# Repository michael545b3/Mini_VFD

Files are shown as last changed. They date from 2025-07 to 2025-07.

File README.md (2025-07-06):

# Mini VFD based on STM32

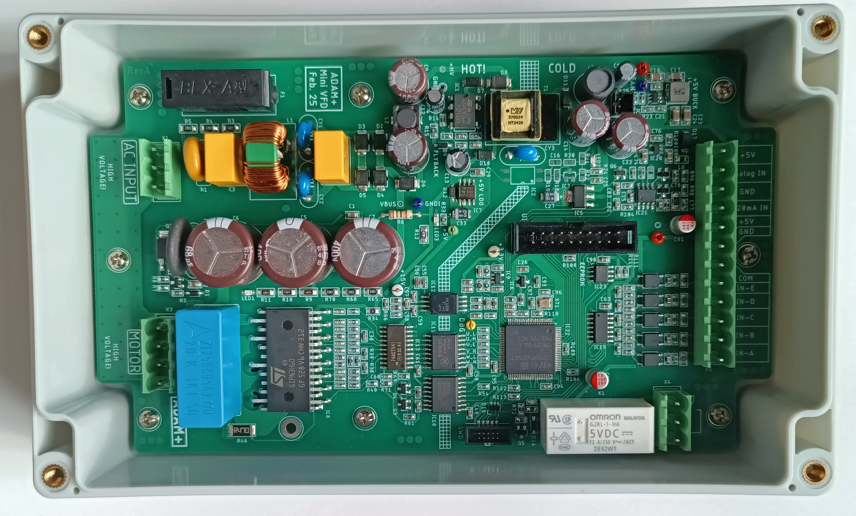
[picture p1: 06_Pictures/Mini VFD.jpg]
Mini VFD


This project is a compact Variable Frequency Drive (VFD) built around an  
STM32 microcontroller and an ST IPM (Intelligent Power Module).  
It is designed to control small AC motors efficiently and safely in a compact form factor.

---

## Hardware Overview

### Core Components
- **STM32F407** microcontroller
- **STGIPN3H60** IPM (Intelligent Power Module)
- **High-voltage measurement**
- **Analog inputs** for control signals
- **Opto-isolated digital inputs**
- **Relay output**
- **EEPROM** for parameter storage

### Power Supply
- **Flyback converter** for isolated supply
- **E-Fuse** for protection
- **Buck converter** with **LDOs** for logic power

### User Interface
- **LCD display**
- **Push buttons** and **rotary encoder** for input

---

## Software Status

The firmware is currently under development. As a hardware-focused developer,  
progress is steady but slow — writing robust embedded software takes time.

So far, the implemented functions run reliably, and more features are being added continuously.  
A demonstration video will be available soon.

---

## Roadmap / To-Do

- [ ] Motor control tuning
- [ ] UI menu system improvements
- [ ] Fault monitoring and protection
- [ ] IO implementation

---

## Contributions

Contributions, feedback, or suggestions are very welcome!

---

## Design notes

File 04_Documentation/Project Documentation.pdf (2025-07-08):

# Mini VFD

Michael Adam
michael.adam4@proton.me

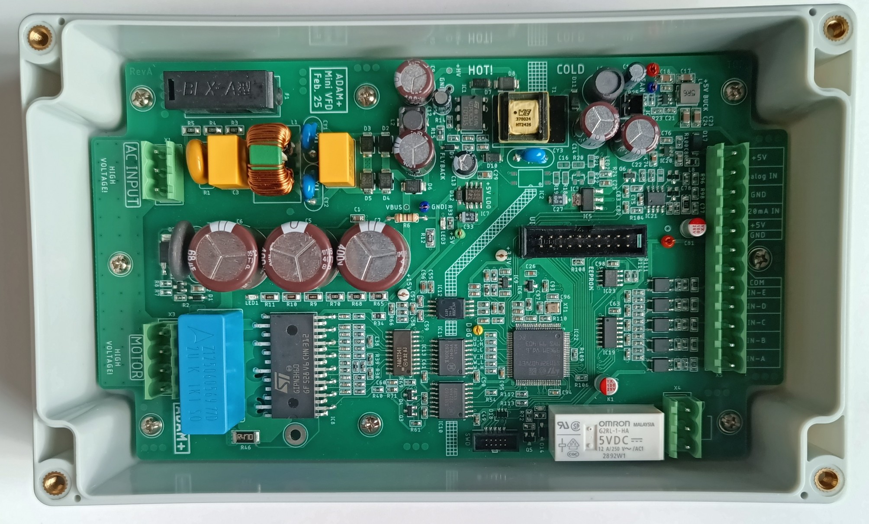
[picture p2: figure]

## General

I've always been fascinated by VFDs (Variable Frequency Drives), but never had the opportunity to develop one professionally, as I don’t work in that field. This project represents my personal journey of building a VFD more or less from scratch. Along the way, I’ve made good use of various helpful application notes provided by IPM (Integrated Power Module) manufacturers, which have greatly supported the development process.

This is a completely independent project — there’s no sponsorship or external funding involved. All components were purchased from LCSC, DigiKey, and AliExpress.
You're very welcome to use, study, modify, and build upon the information, schematics, code, and ideas shared in this project. If you publish your own work based on it, I’d appreciate it if you mention me as the original source. That said, everything here is shared as-is, and free to use – in the spirit of learning, transparency, and open hardware.

## Important

⚠ Safety Notice
Please note that this project involves high voltages (up to and beyond 325V DC), high currents, and components that can pose serious hazards if mishandled. This is not a beginner-friendly project. Anyone attempting to replicate or modify it must have a strong understanding of:
- Electrical safety and protective measures
- Power electronics
- Isolation techniques
- Thermal management and safe power supply design
Always work with proper protective equipment, use an isolation transformer, and perform tests with care. You are fully responsible for your own safety.
⚠ Disclaimer
This project is provided for educational and experimental purposes only. I am not liable for:
- Any damage to equipment, hardware, or software
- Any kind of personal injury, electric shock, fire, or property loss
- Any unintended consequences arising from the use, misuse, or misunderstanding of the content
You use this material entirely at your own risk. No guarantee is made that the circuits or designs will work reliably, safely, or under any specific conditions. Especially the software is still work in progress.
⚠ Compliance
The final device has never seen the inside of an EMC lab! It would most likely fail most of the tests (just like many reference designs from reputable manufacturers, by the way).

## Design Concept

Since this is a pure DIY project, there were no strict specifications. But there are still some, to have an idea and plan to stick to it. The main specs are:
- Design for tiny motors around 1A per phase
- 230V AC Input (could also be a universal input)
- LCD Display
- Output Frequenvy up to 150Hz
- Over current protection
- Voltage Sensing
- Fused Aux Output
- Digital/ Analog Inputs
- Easy to solder parts for easy rebuilds (no BGA, QFN etc…)
- Transparent enclosure
On the picture bellow you can see a very rough concept of the VFD:

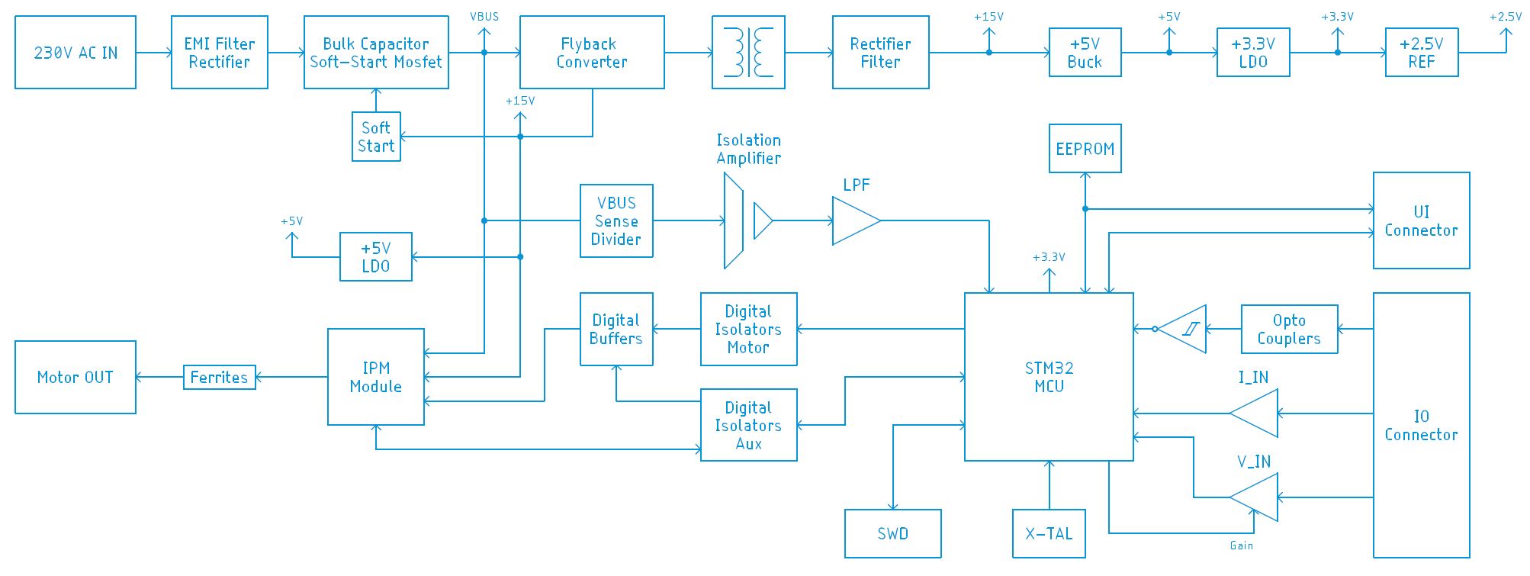
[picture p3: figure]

It’s pretty straight forward: the mains AC voltage goes through the EMC filter to the rectifier, after rectification to the bulk capacitors, the bulk capacitors are equipped with a soft-start circuit, that bypasses an NTC at the negative pole of the capacitors. The fly-back converter supplies both the secondary and primary side with auxiliary voltages. On the primary side there is a 15V rail, needed for the IPM module, and on the secondary side, a very unprecise voltage, that gets converted into a stable 5V rail. LDO’s are regulating the voltages to logic levels (5V @ primary and 3.3V @ secondary). The IPM has two supplies, one VBUS (325V) supply and an auxiliary 15V supply for the internal gate drivers. Signals to the IPM are coming from the MCU, through some digital buffers for safety, isolated by digital isolators. There are two digital isolators, one for the motor signals and one for other miscellaneous signals. To the able to adjust the motor’s voltage, we need to monitor the VBUS rail, this is realized with a potential divider, an isolating amplifier and some filtering and signal adequating in front of the ADC within our MCU. The brain of our VFD is an ARM Cortex M4 STM32F407 microcontroller, which might be an overkill for the tasks it has to do, but it’s better in my case to oversize something and have enough headroom to expand the functionality. An external I2C EEPROM is being used to store user parameters. Optocouplers are isolating the digital inputs. The analog signals are going through some protection to opamp buffers and then to the MCU’s ADC.

## Circuit Description Mainboard

AC Input section:

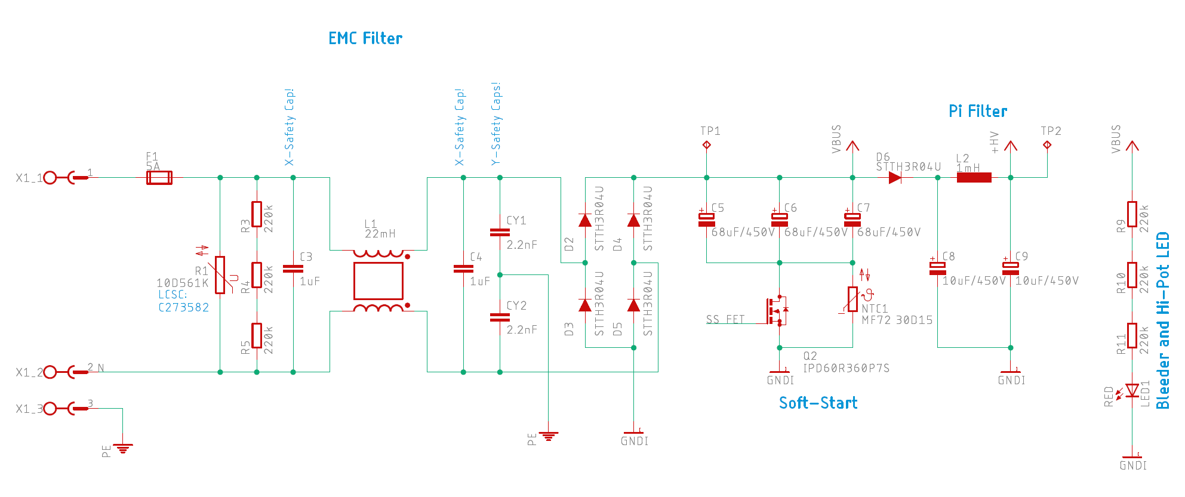
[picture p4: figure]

EMC filter on the left, discrete diodes bridge rectifier and some electrolytic s that have a soft-start circuit. When the device is powered the Mosfet is open and the NTC righ resistive, after around 130ms, the Mosfet closes and bypasses the NTC. VBUS goes directly to the IPM. A Pi filter is placed between VBUS and the fly-back circuit, to reduce noise coming from the fly-back converter. An LED shows if there is high potential at the caps and at the same time discharges them.
Soft Start delay circuit:

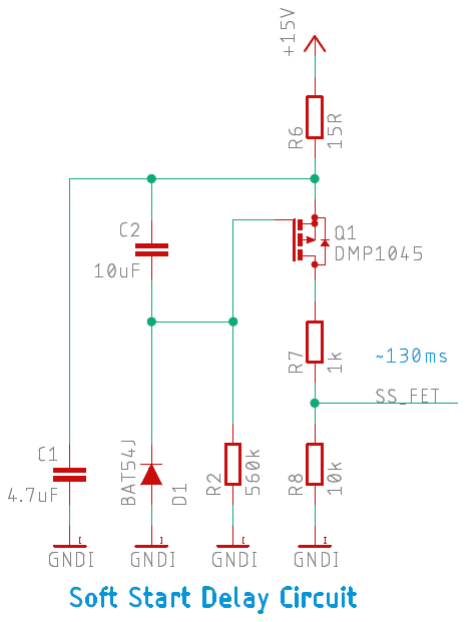
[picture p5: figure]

The small circuit above, is a quick and dirty way how to add some delay to bypass the NTC.

Flyback converter:

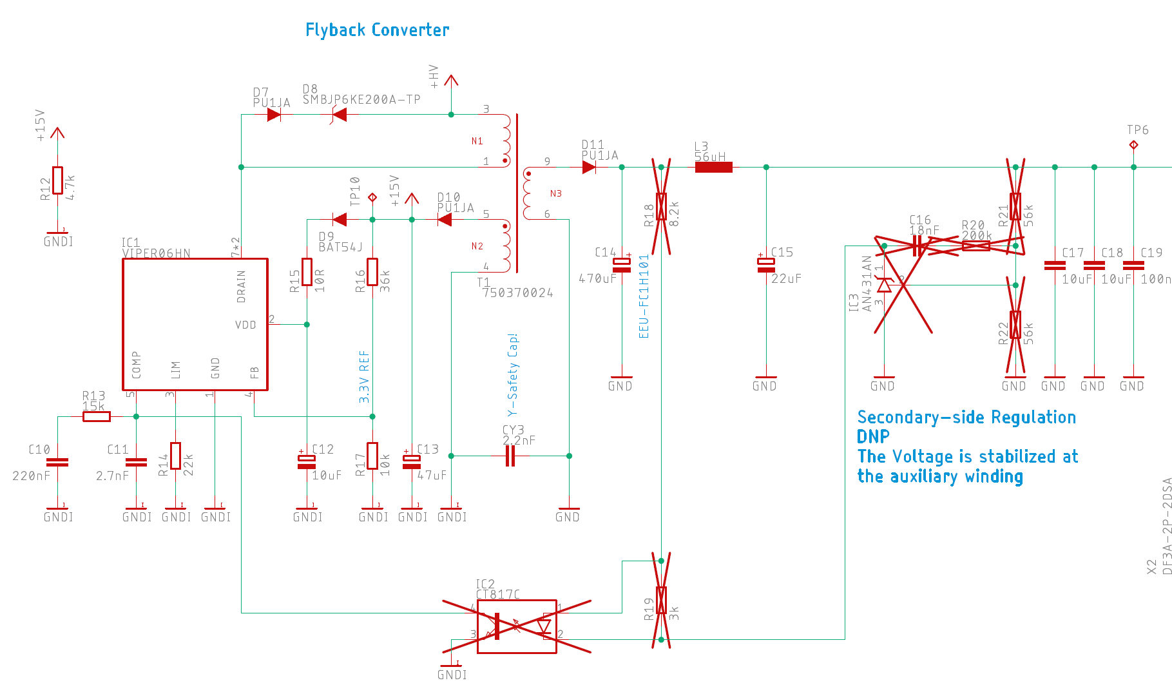
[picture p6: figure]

The fly-back converter supplies the primary side with a clean and regulated 15V and the secondary with something around 12V, the primary side regulation is not really working that great, but we can catch it in the buck converter. Secondary side regulation is placed on the board, but not populated, I am more interested in a clean auxiliary voltage rail on the primary.

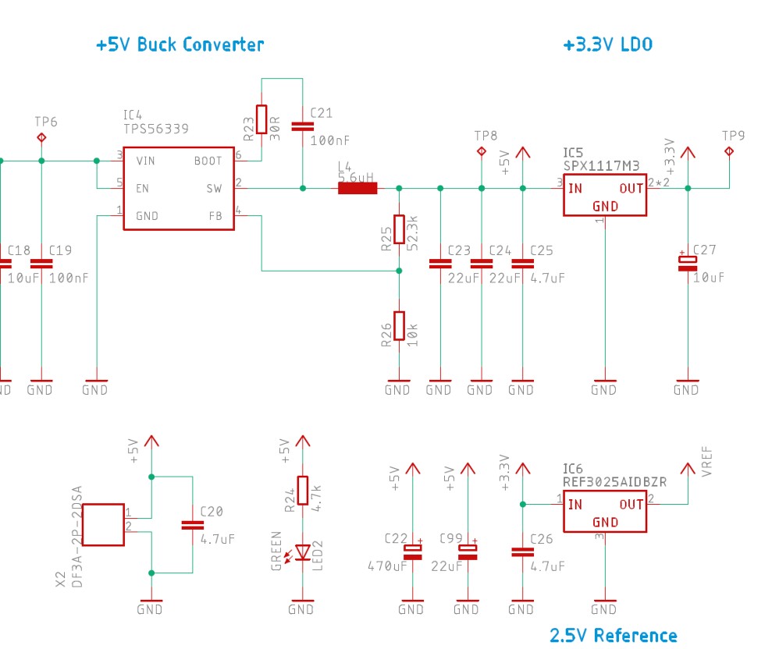
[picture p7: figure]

Simple synchronous buck converter, all values were calculated by Texas Instruments’ WEBENCH. Small LDO for the 3.3V rail and a reference that goes to the ADC’s reference pin of the MCU.

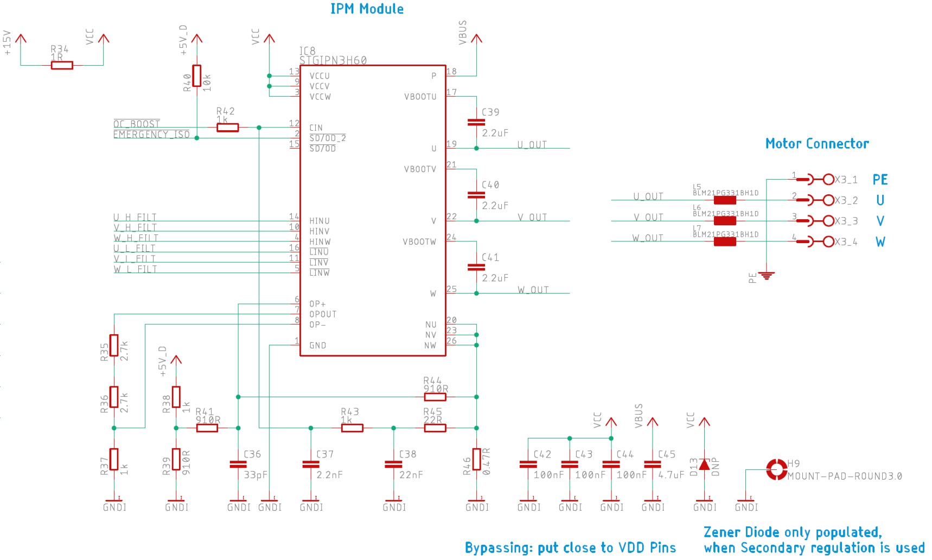
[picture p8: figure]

IPM Modules are just perfect for these kind of projects. No Gates to drive, no slopes to control, everything is done internally, we just input logic values and that’s more or less it. It is crucial to bypass the IPM in the correct way, as described in the data sheet and application notes. C42-C44 are bypassing the 15V Rail and a big 4.7uF foil capacitor C45 does the same for VBUS. Before going out to the motor connectors, there are some ferrite beads to filter out at least some of the high frequency content, coming out from the IPM. Be aware U_OUT, V_OUT and W_OUT are going with very high dv/dt from 0V to 325V! Remember, in the «real world», the motor cables must be as short as possible and the VFD as close as possible to the motor! The best case if the VFD sits directly on top of the motor, so all the high frequency noise stays inside the metal housing of VFD and motor.
The used IPM is more made for something like HVAC and other machines, where the VFD is integrated in the device, and less for a standalone VFD. But since this project is more a demonstrator than an actual product, it’s fine. Therefore it has some built in over current protection, we just have to add some passives externally. This part of the circuit has not yet been fully tested and tuned! The values have been taken from data sheets and application notes.
Some auxiliary circuits on the hot side:

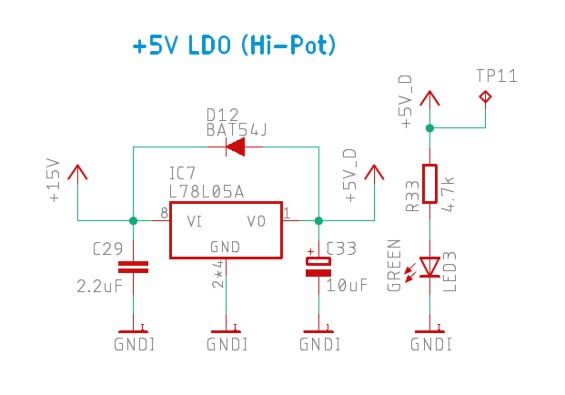
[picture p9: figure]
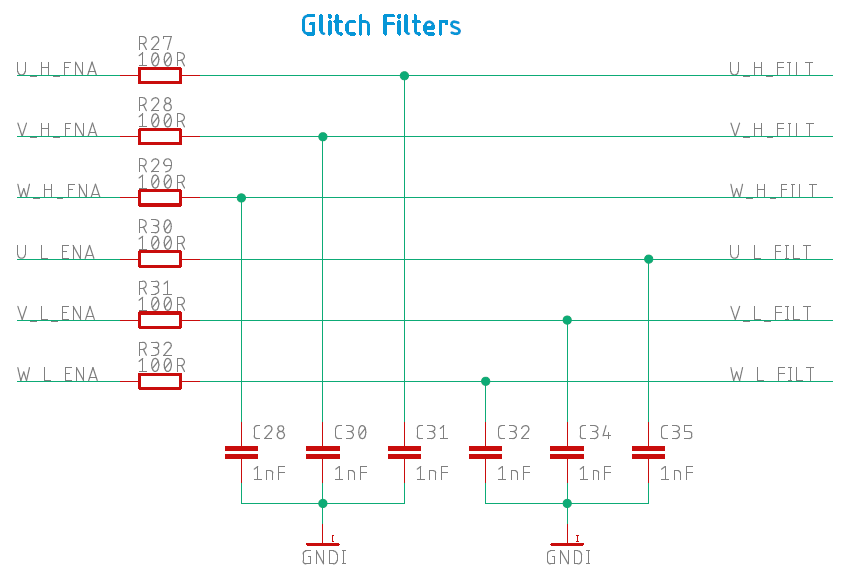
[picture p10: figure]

Nothing special here, just some low pass filtering, to avoid interference’s on the six control lines. Those lines are critical! A false signal state could damage the IPM or at least disturb the function.

VBUS Sensing:

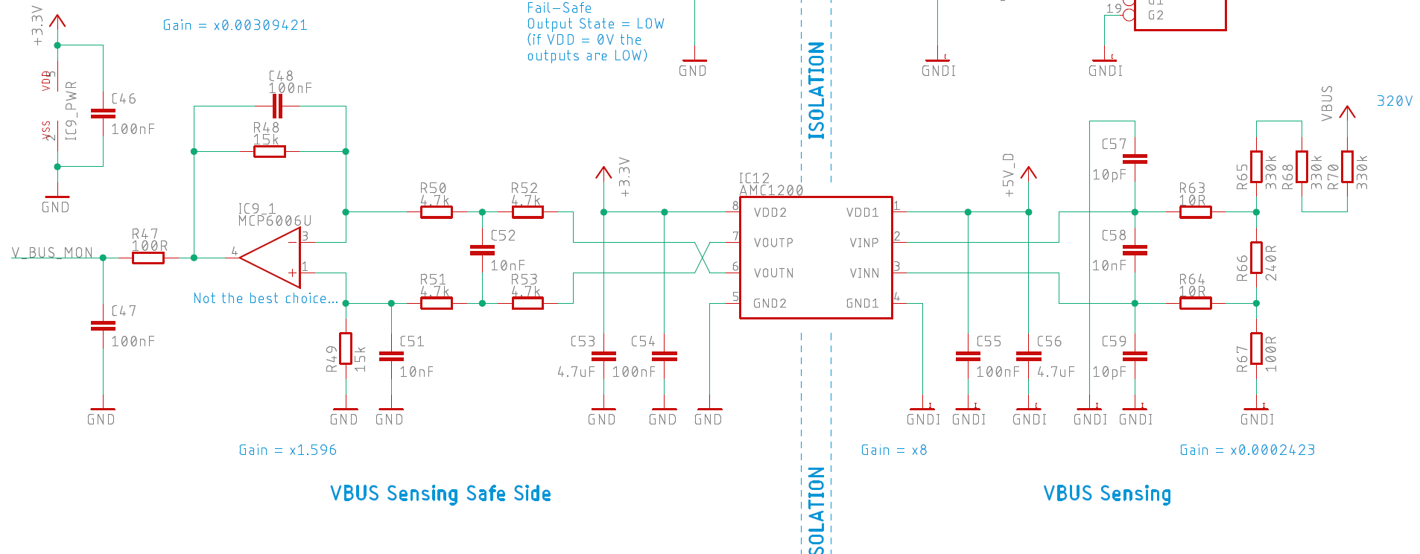
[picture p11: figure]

VBUS, which is around 325V DC @230V AC input, has to be attenuated first by a gain of x0.0002423, before going into the isolation amplifier, which has a gain of x8. The final stage before the ADC has a gain of other x1.596, so the resulting gain is x0.00309241. @325V DC, we get around 1V at the output, going to the ADC, which is not that great, since the reference is 2.5V, so there is some of the ADC range lost, but it should be enough. The passives are filtering unwanted frequencies and transients. The opamp is not the best choice, I just had it lying around.
Digital Isolators:

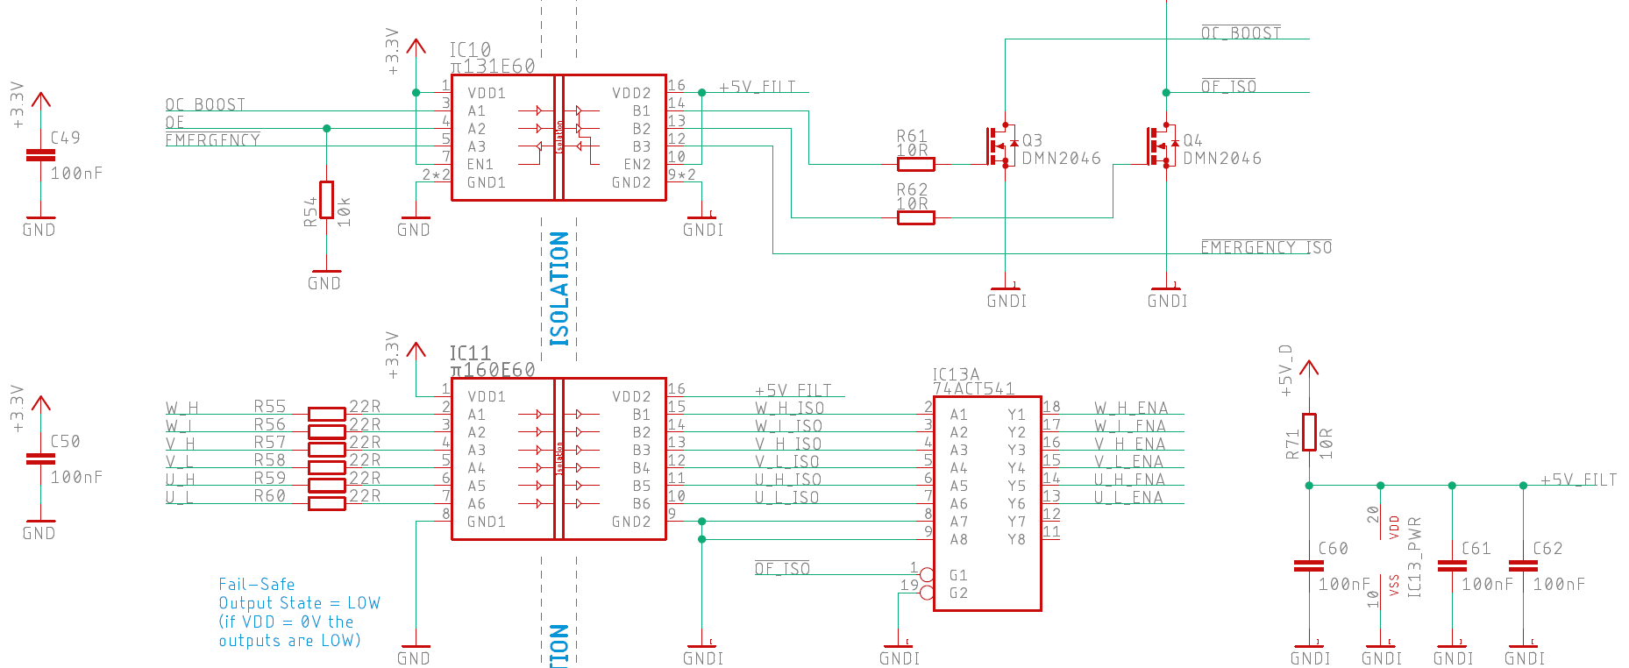
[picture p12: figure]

These digital isolators are safety critical parts, they isolate secondary from primary. 74ACT541 is a digital buffer, which is being enabled when the VFD is enabled.

Analog Inputs:

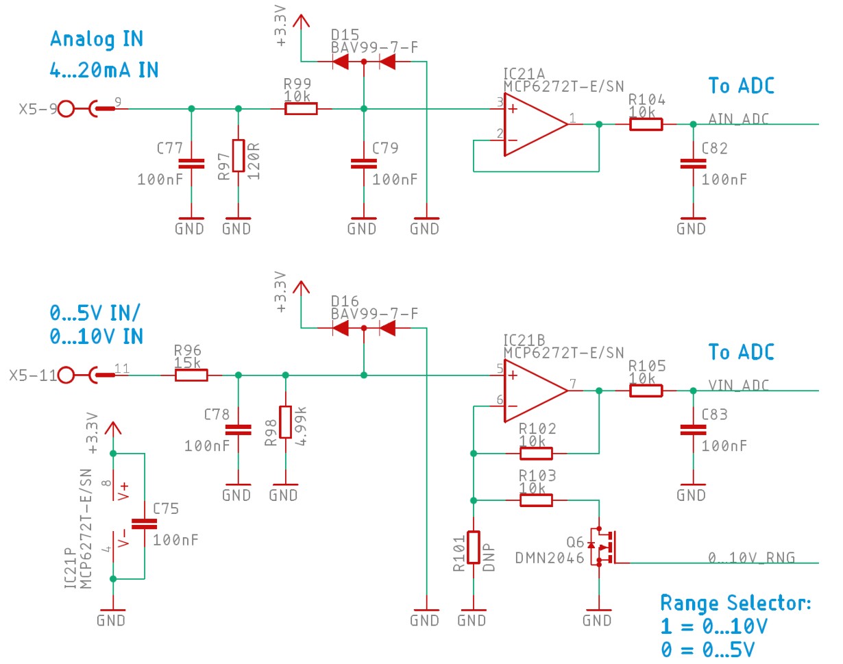
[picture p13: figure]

R97 acts as a I-V converter, the resulting voltage is getting filtered, buffered and goes through an other filter to the ADC. With the voltage input, it is a bit more complicated. VFD’s usually have 0...10V analog inputs, which is an industry standard. They also provide 10V, which the user can also connect to a potentiometer and analog input, to control the motor remotely. On the secondary side, the highest voltage is 5V. To not loose ADC precision, there is a range selector, which can change the gain from x1 to x2 of the opamp. So at 0...5V and 0...10V input, the output will be 0...2.5V.
E-Fuse:

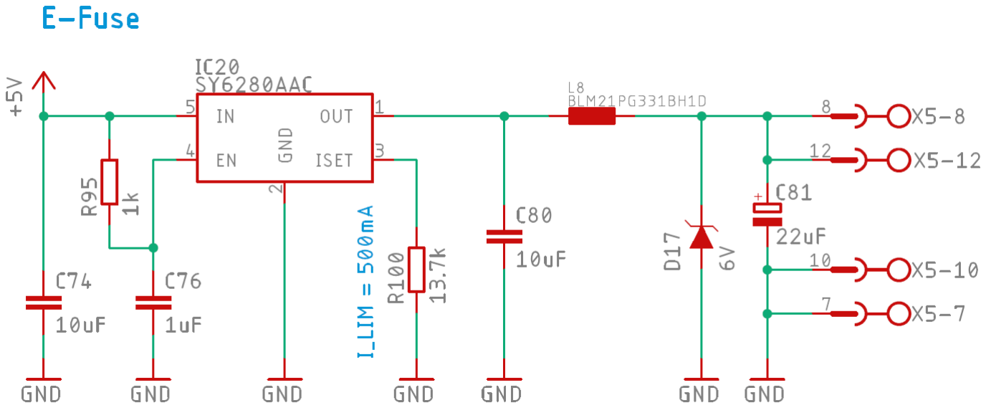
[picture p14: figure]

To protect the internal circuit, there is an E-Fuse, limited to 500mA. A TVS diode protects from ESD pulses.

Digital IO’s:

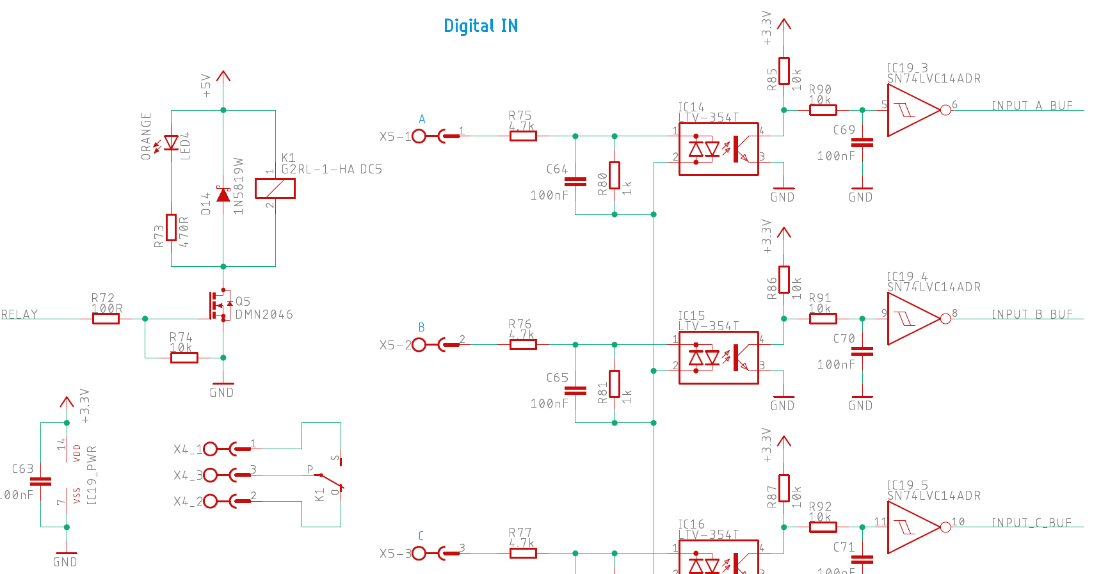
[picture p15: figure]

There is only one by a relay galvanically isolated output. This output can be configured via the GUI, what it should do. Same for the digital inputs. They are all isolated, but not between each other!
Last Page:
Is self explanatory, just an MCU, with an x-tal oscillator, a connector to the user interface PCB and an EEPROM for user parameter storage.

## Circuit Description UI Board

The UI (User Interface) board is mounted at the top cover plate, giving access to a display, 4 illuminated buttons and a rotary encoder. Let’s go through the simple schematic: Debouncing:

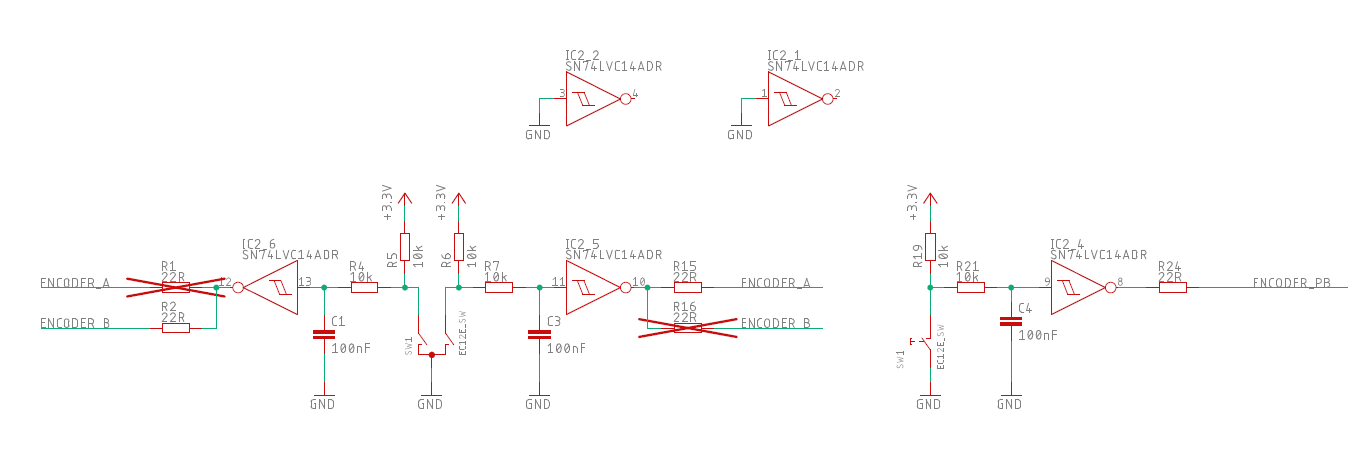
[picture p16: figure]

The debouncing I took very serious for the rotary encoder, I already had some painful experience in the past with them. The 20 cents are well invested in my case. For sure it would be possible to solve it completely in software, but this would have taken a lot of time. Like now, the aggressive filter is getting rid of all the bounces and the schmitt-triggered inverter is converting the banana-like signal into a nice LVCMOS signal. In case the encoder-mode counter in STM32 is counting in the wrong direction, I added an option to change polarity of the encoder, which is much easier than messing around with the code or settings.
Debouncing for the encoder push-button is not necessary, but since there are some inverters free, why not.
IO Expander:

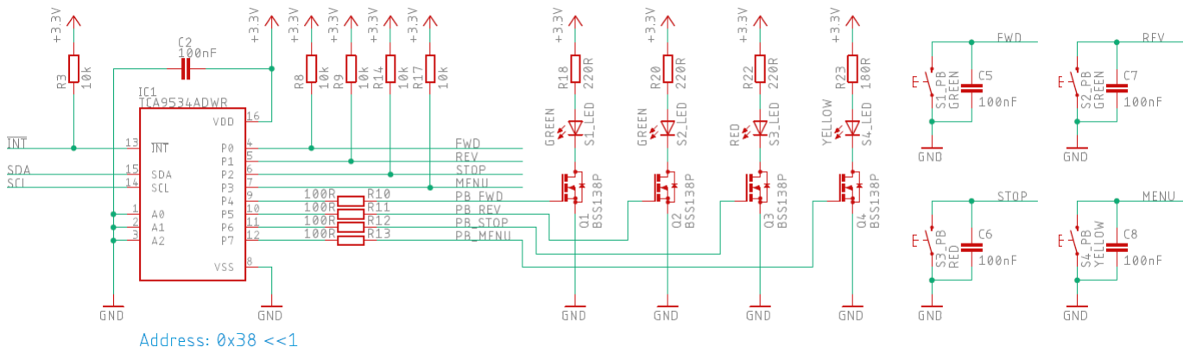
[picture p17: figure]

Through this IO expander, the MCU can poll push-button states and switch the LEDs. The communication protocol to the expander is I2C, which is not ideal, since it could make problems in harsh environments (noise/ transients..), but it this project it is okay.

Display:

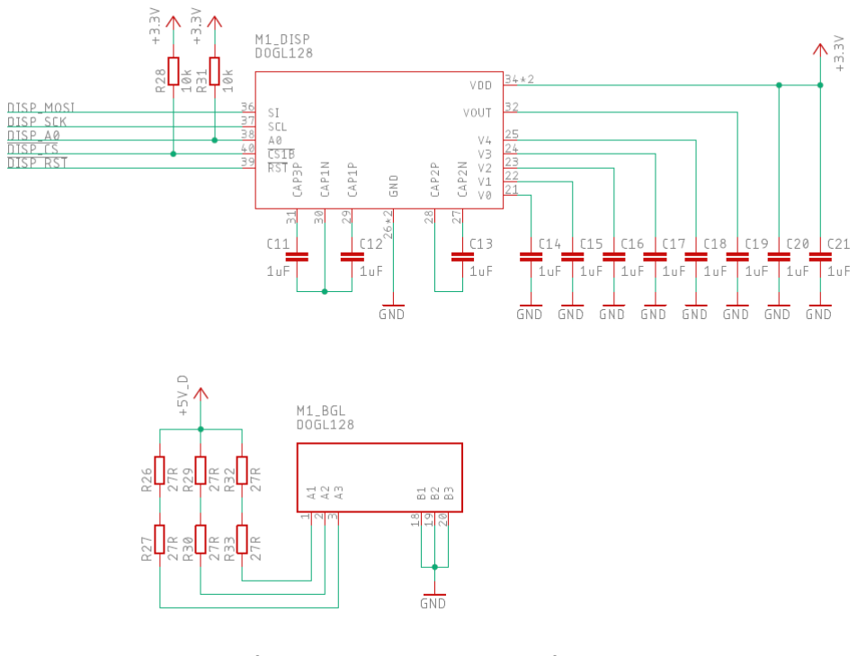
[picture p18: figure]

I use a DOGL128 LCD clone from Aliexpress. They work so far as good as the originals. Just the background light is original, ordered from Digikey. The datasheet precisely describes, how to connect and drive the LCD. To avoid glitches during MCU reprogramming, I added pull-ups to the A0 and #CS lines.

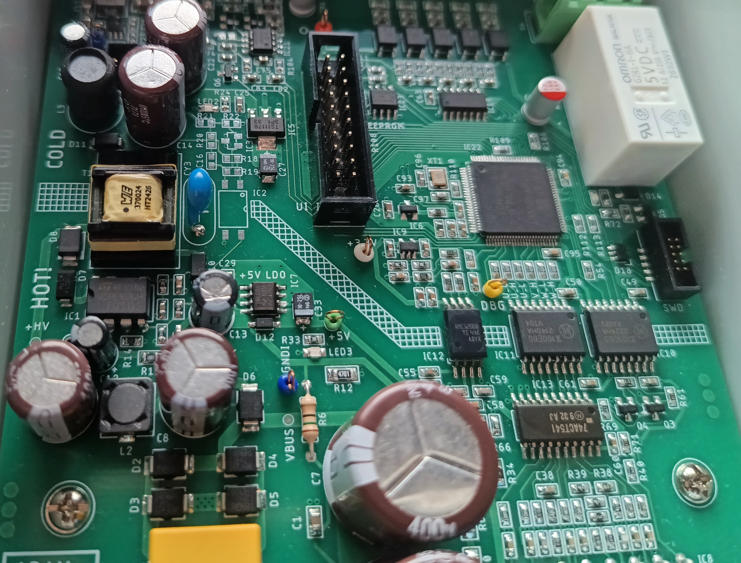
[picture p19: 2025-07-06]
06_Pictures/Mini VFD Detail PSU.jpg

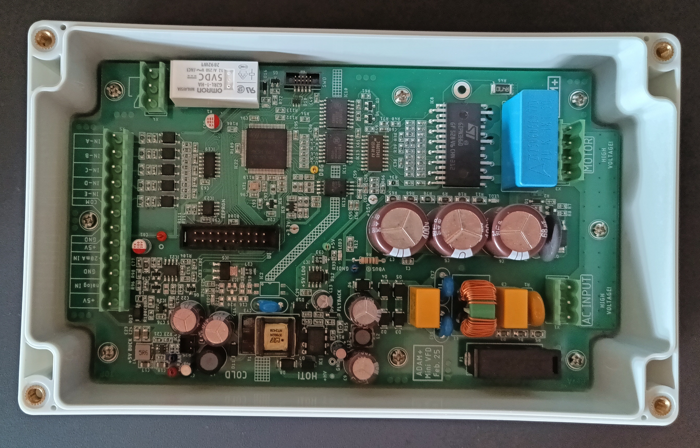
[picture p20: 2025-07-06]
06_Pictures/Mini_VFD_Top_View.jpg

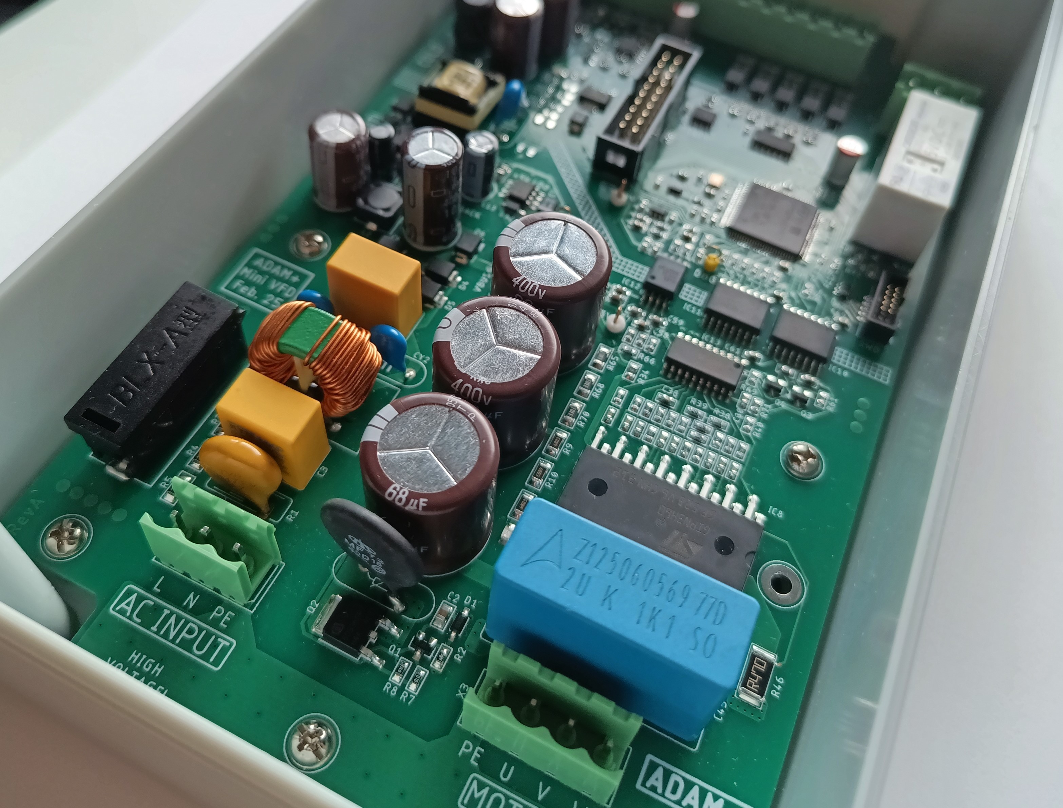
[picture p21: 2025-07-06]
06_Pictures/Mini VFD Detail IPM.jpg

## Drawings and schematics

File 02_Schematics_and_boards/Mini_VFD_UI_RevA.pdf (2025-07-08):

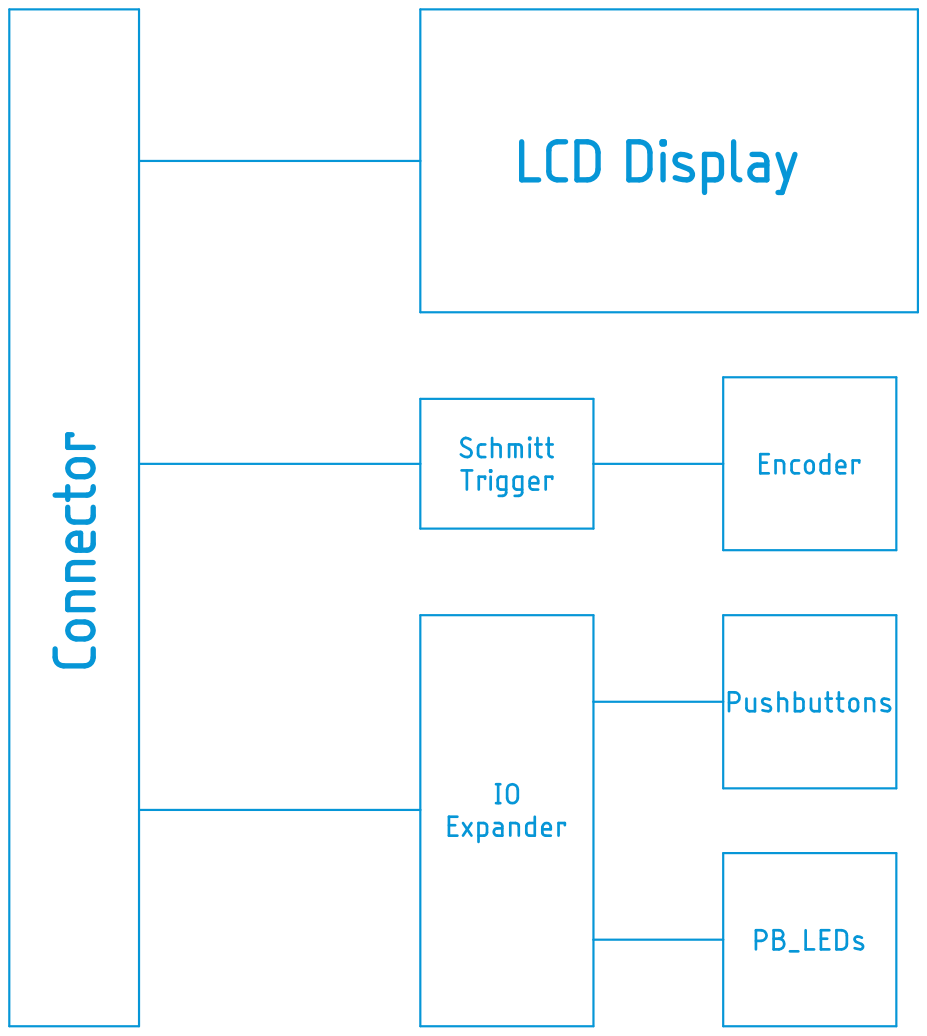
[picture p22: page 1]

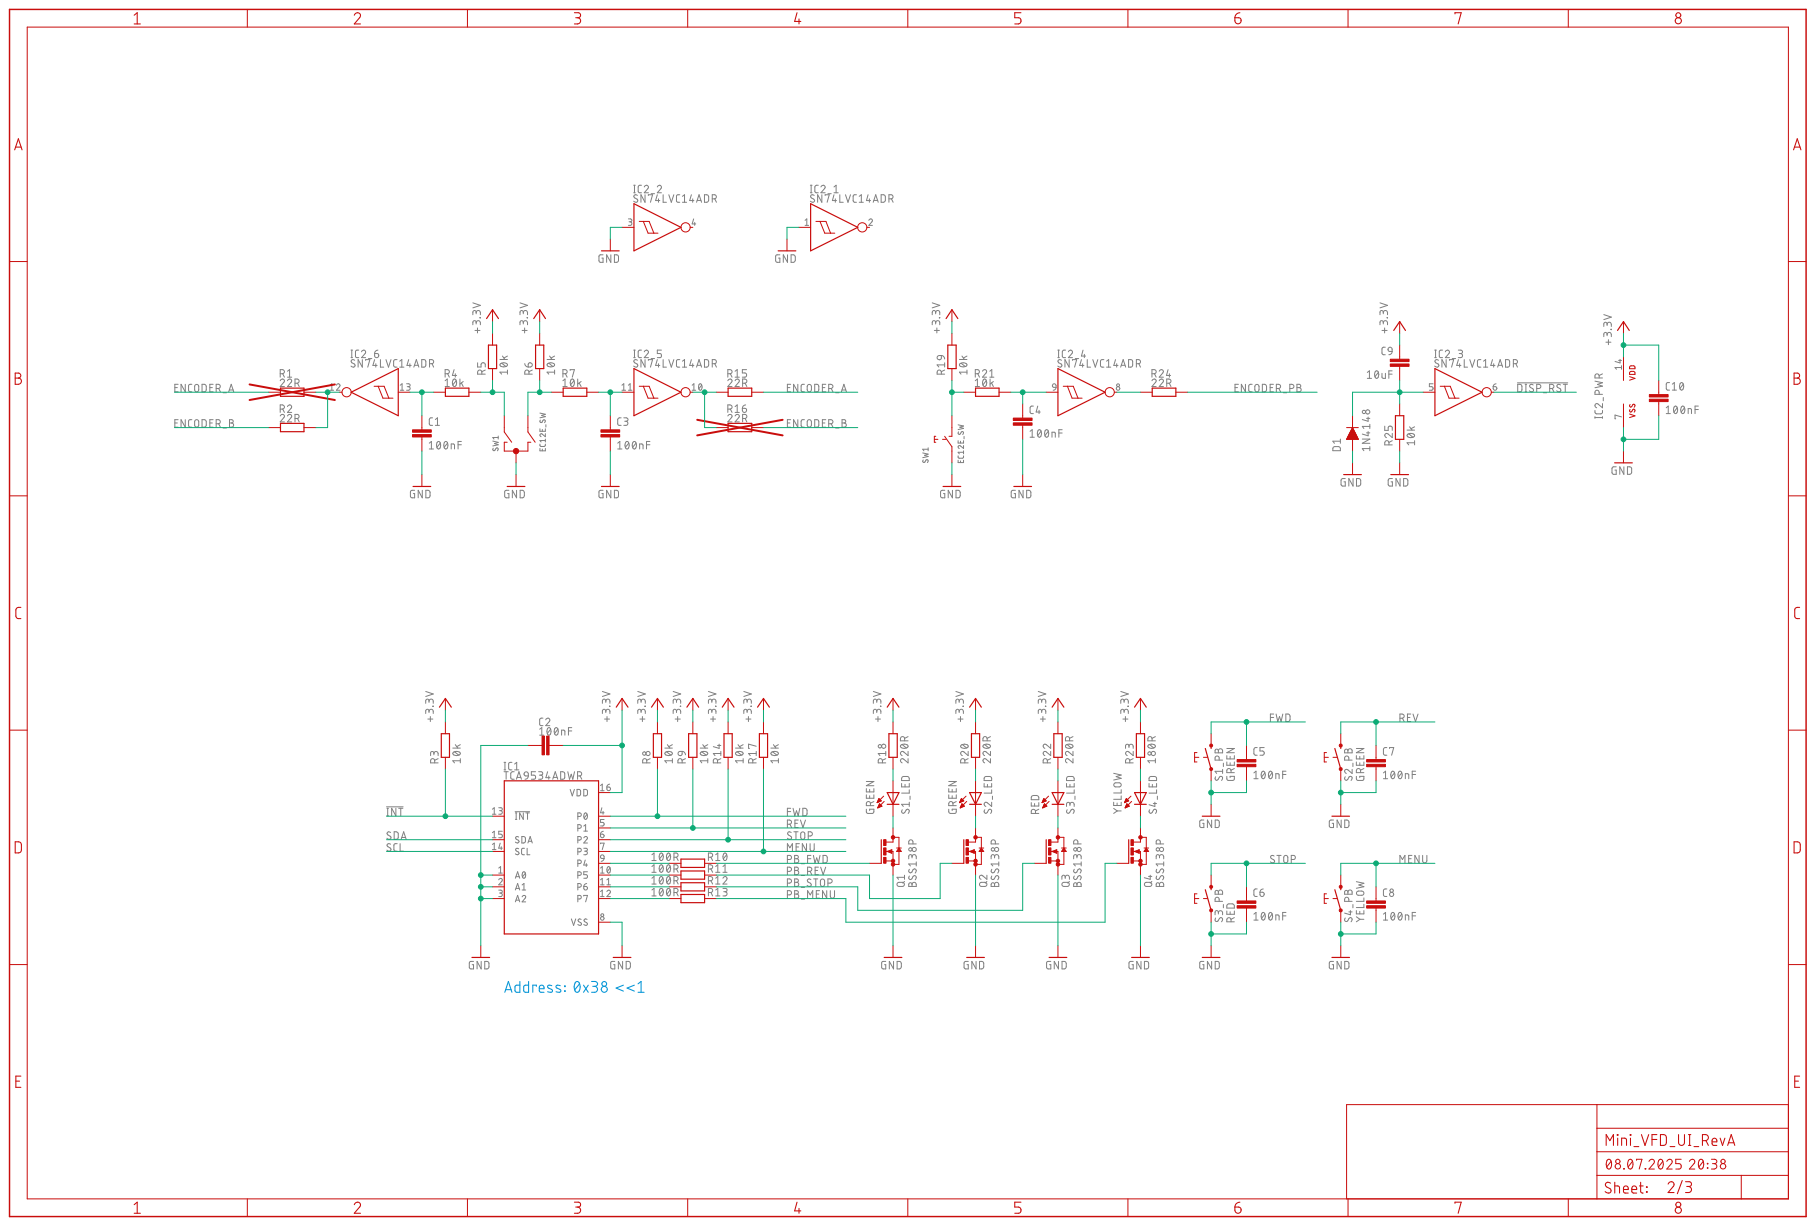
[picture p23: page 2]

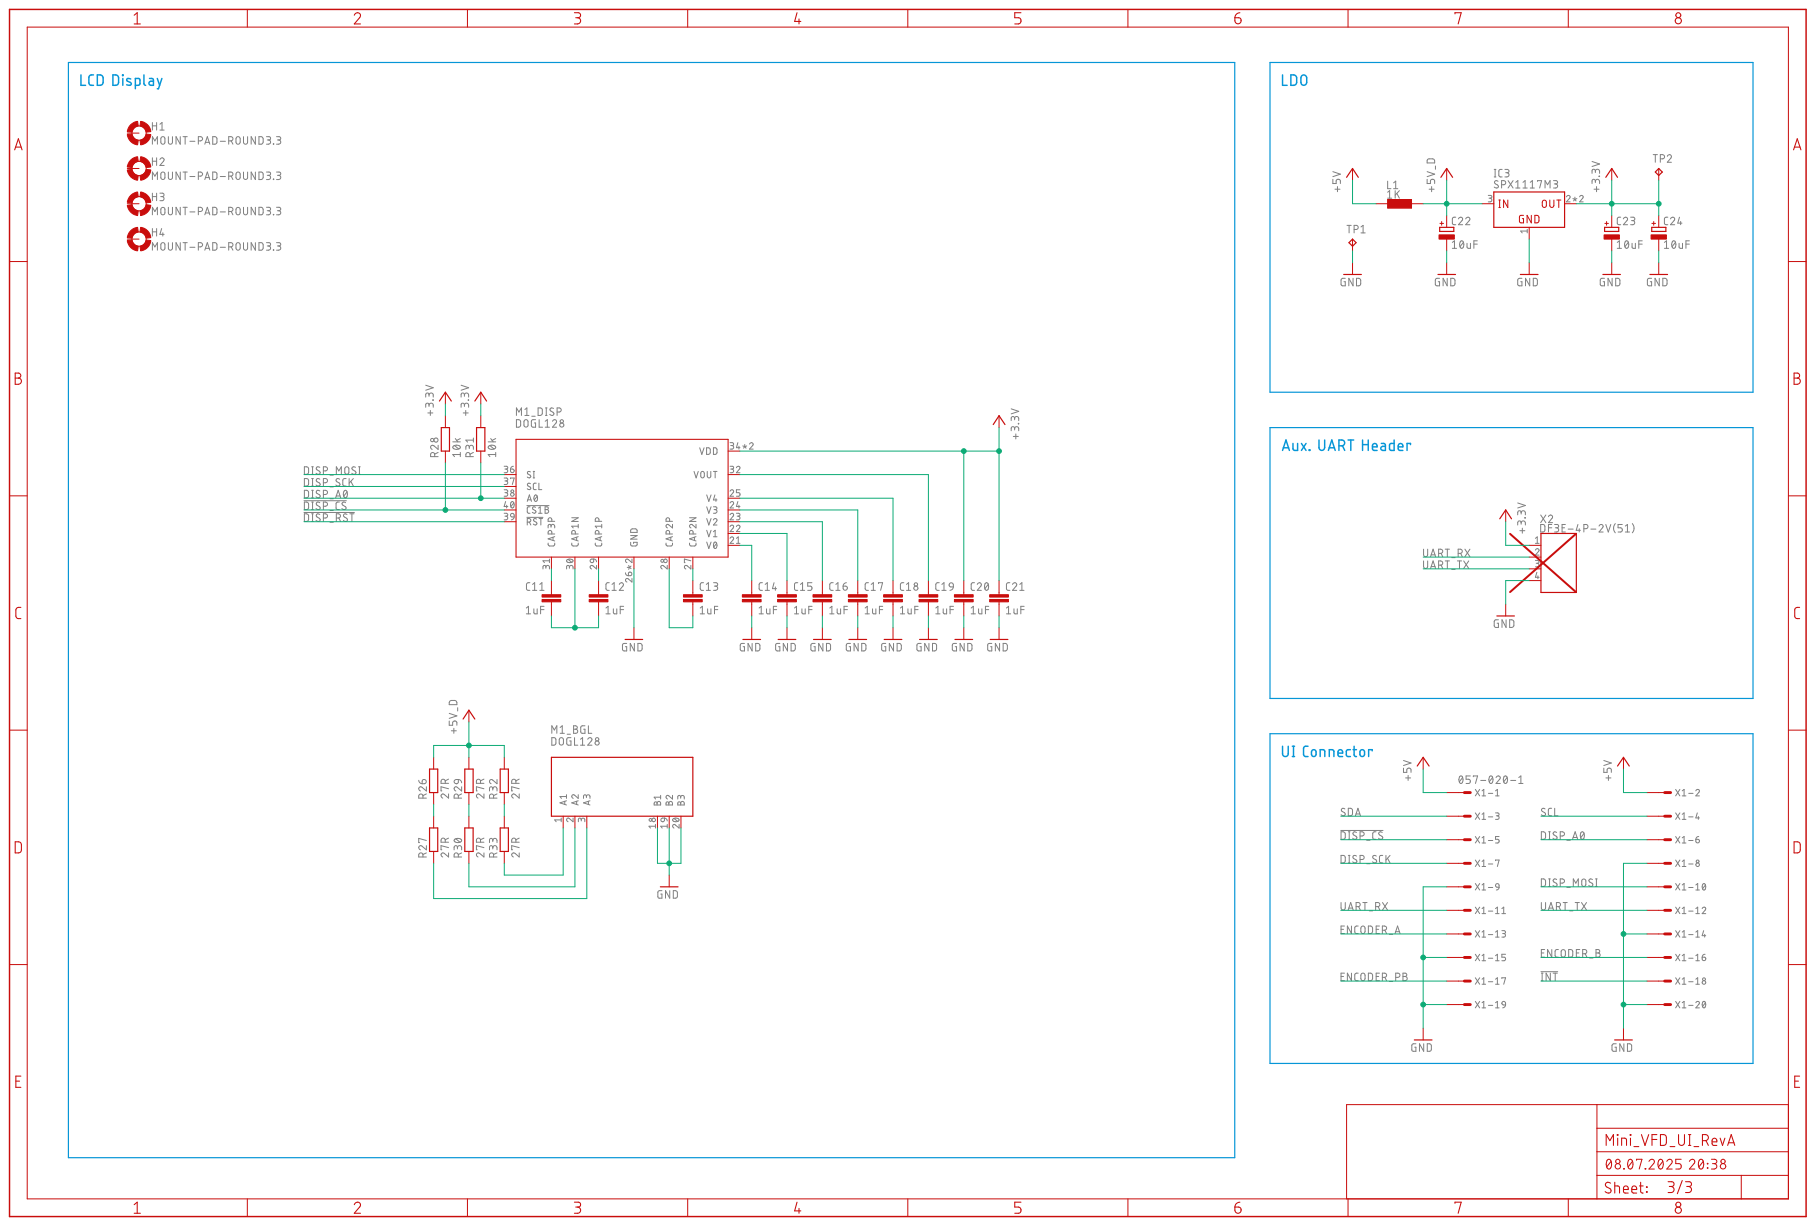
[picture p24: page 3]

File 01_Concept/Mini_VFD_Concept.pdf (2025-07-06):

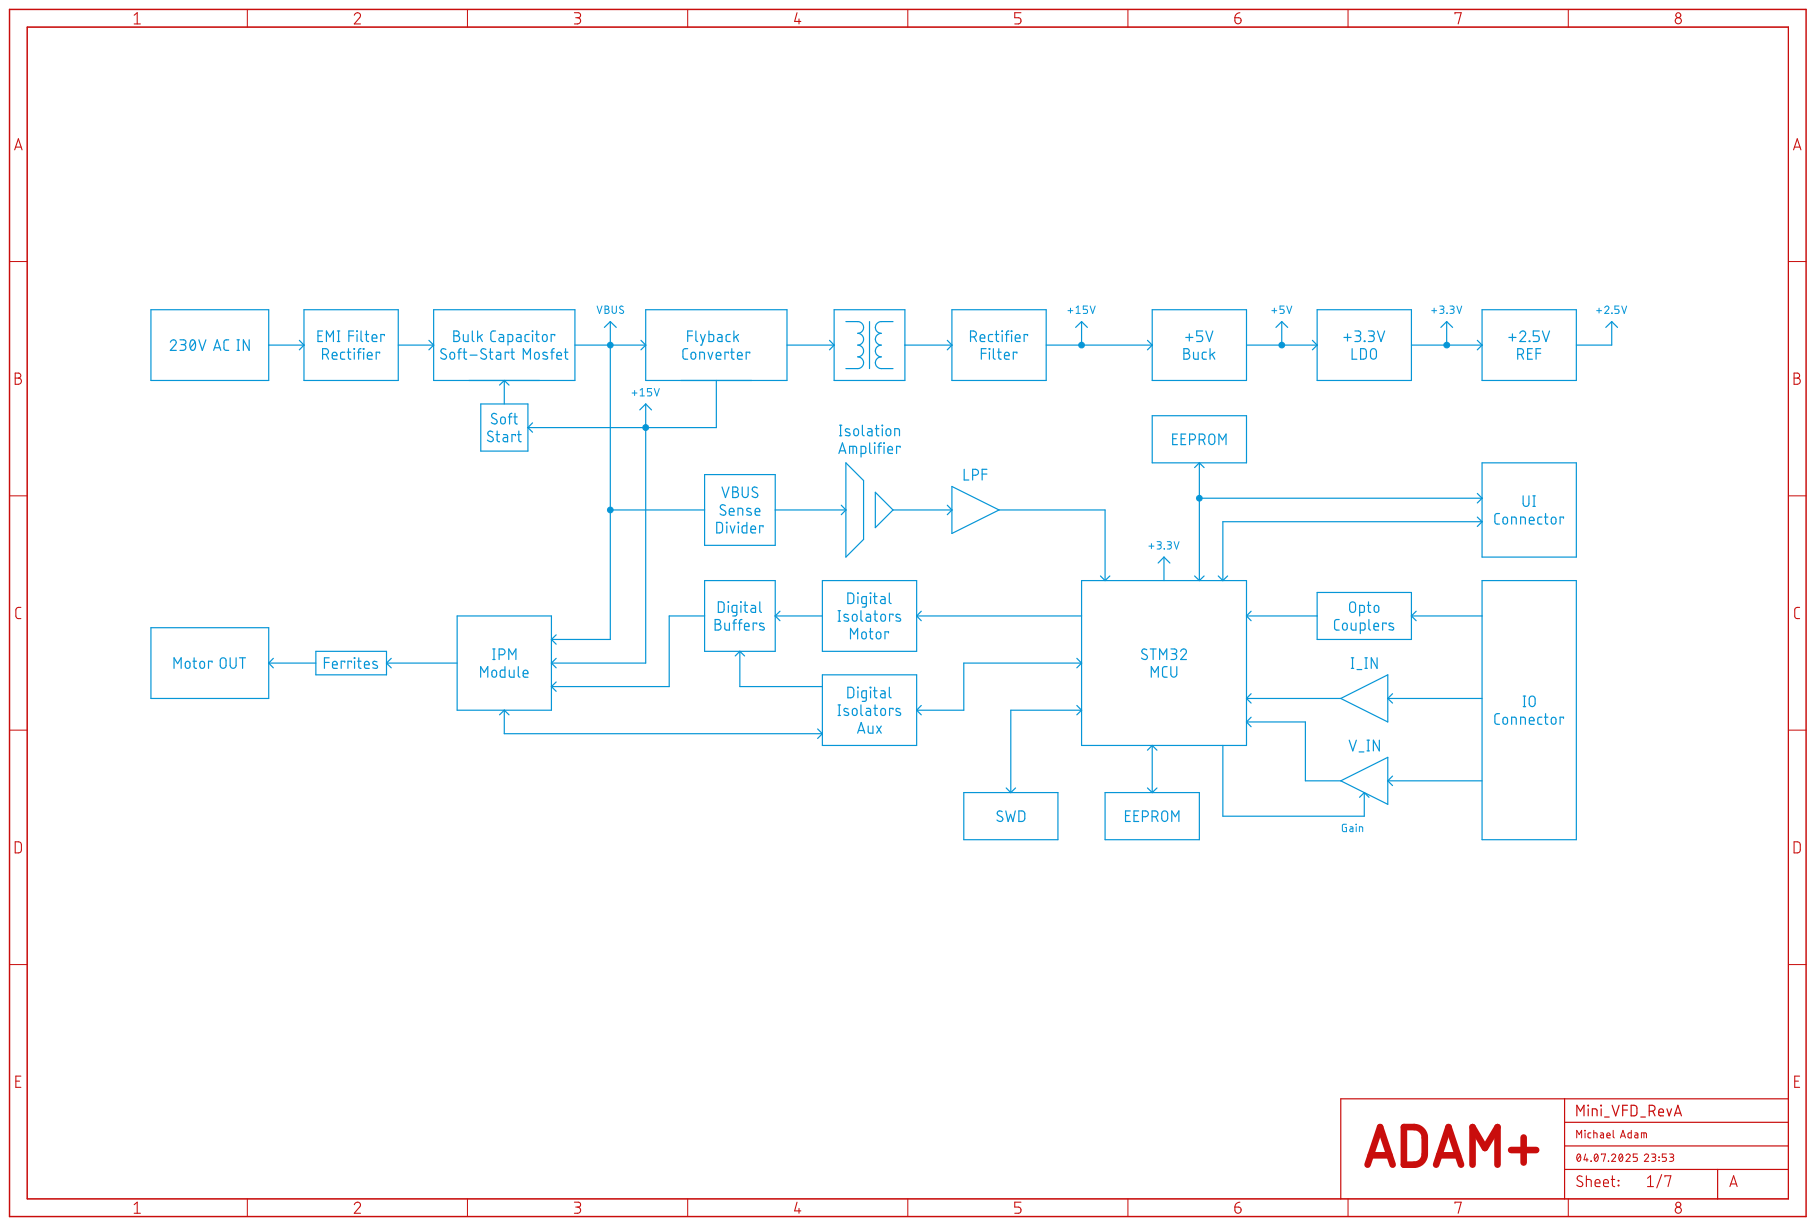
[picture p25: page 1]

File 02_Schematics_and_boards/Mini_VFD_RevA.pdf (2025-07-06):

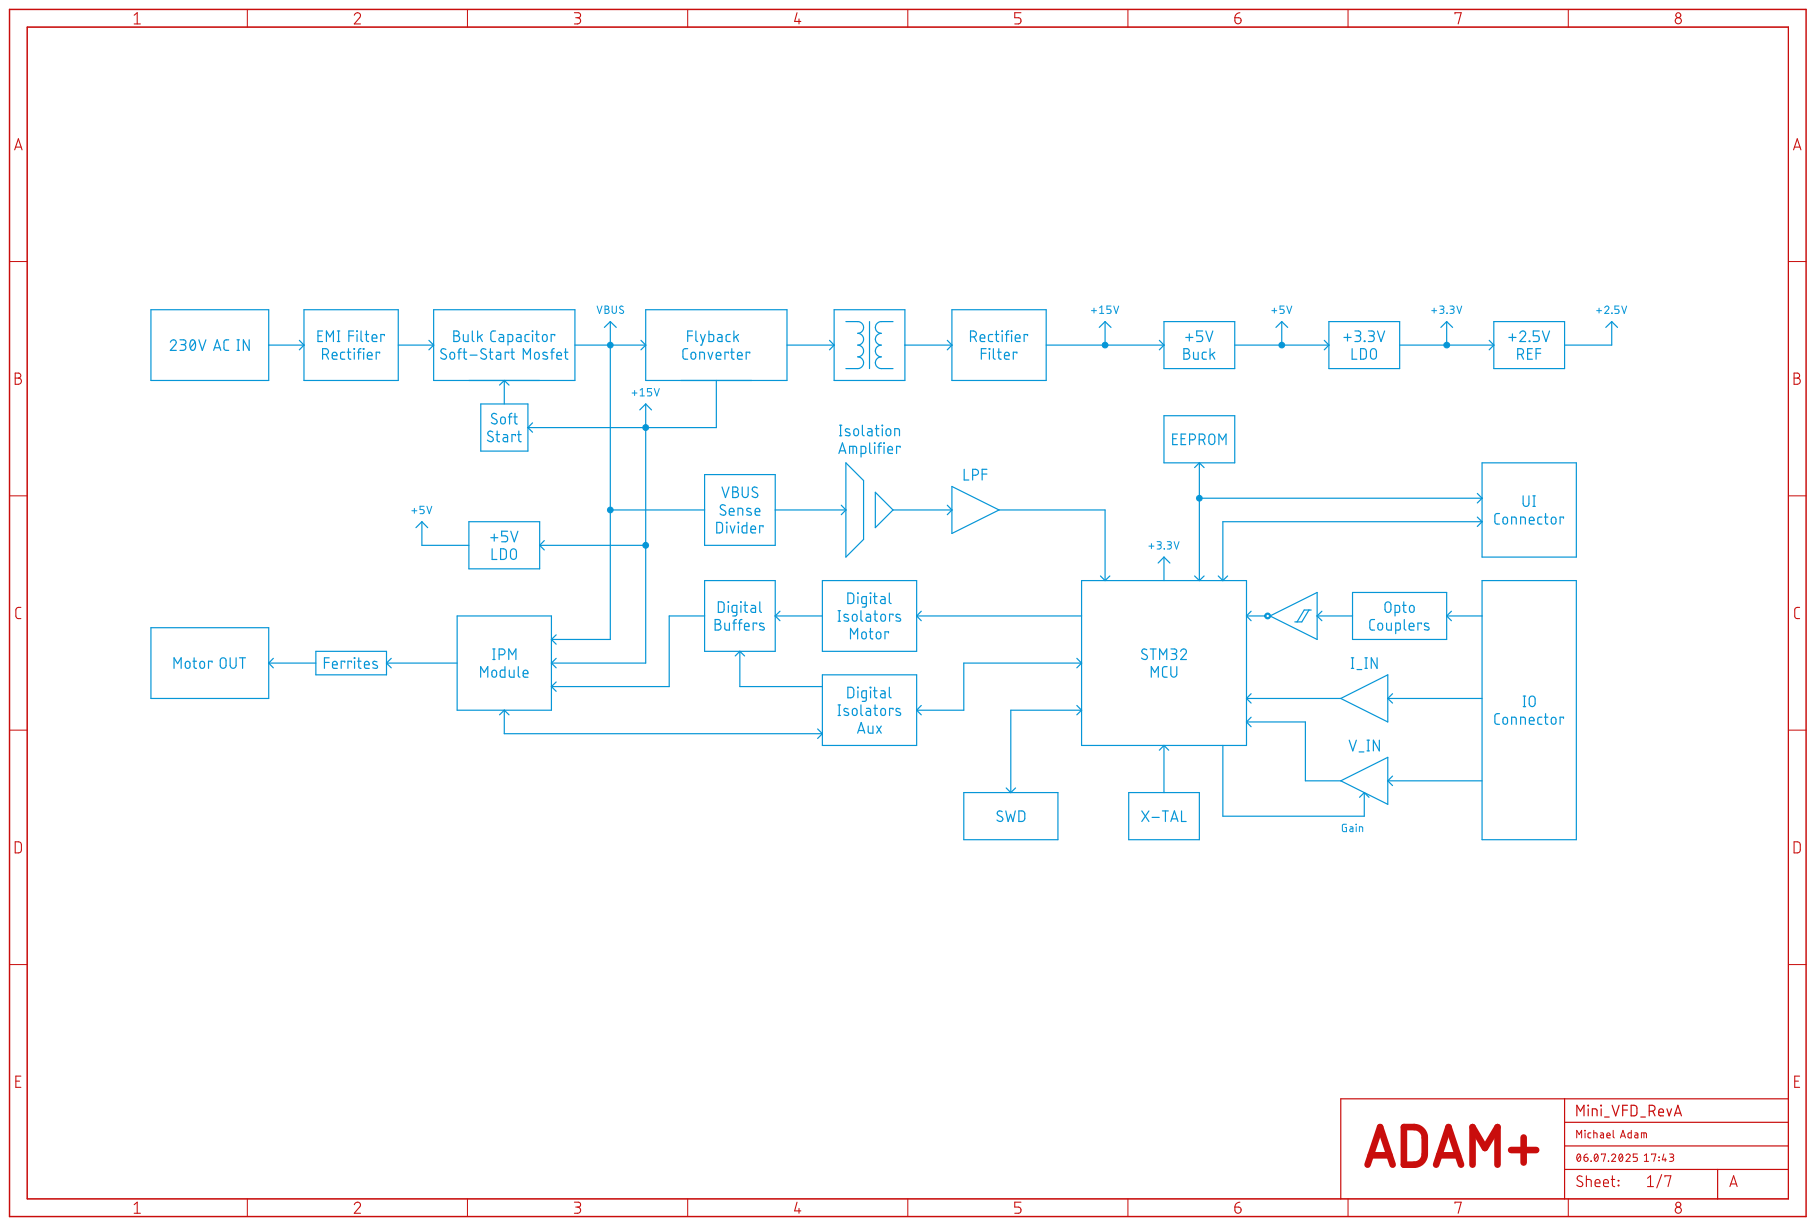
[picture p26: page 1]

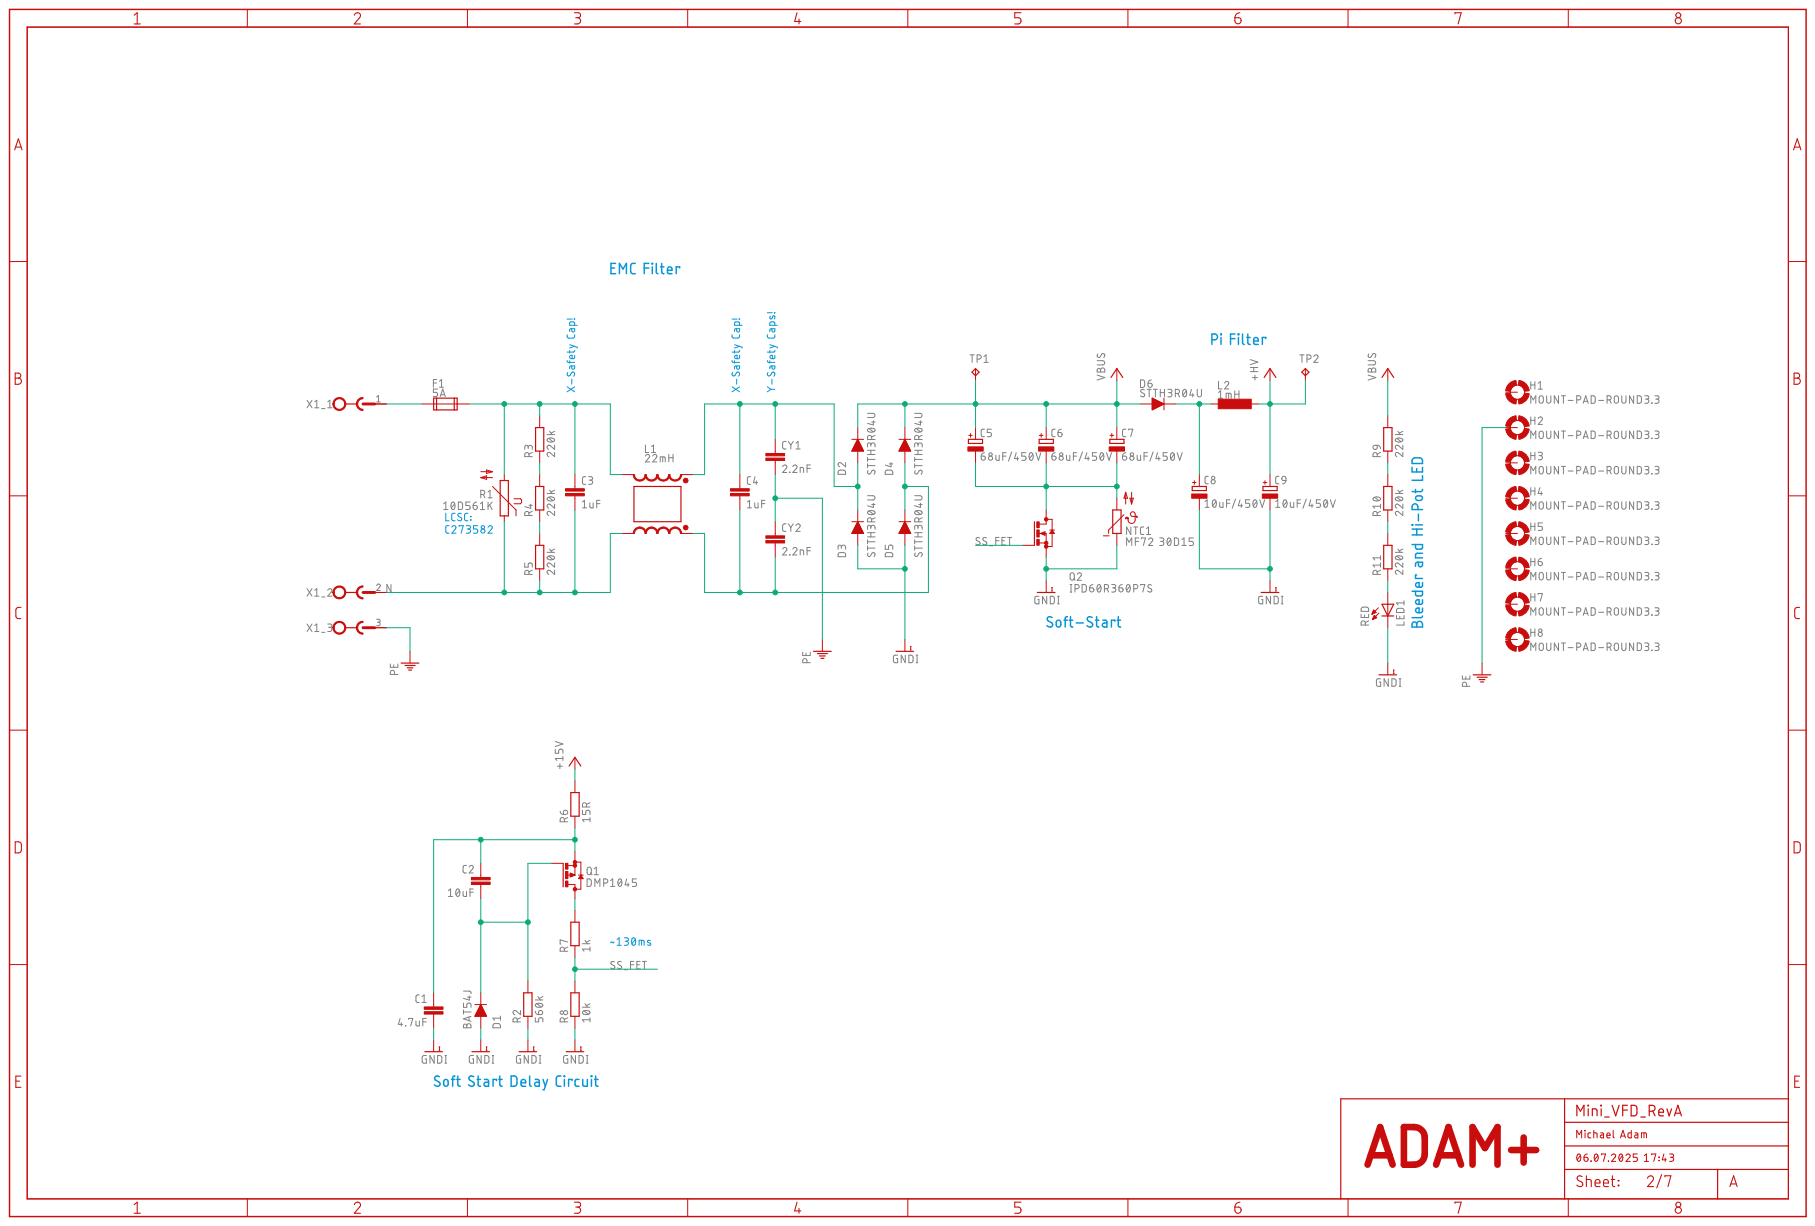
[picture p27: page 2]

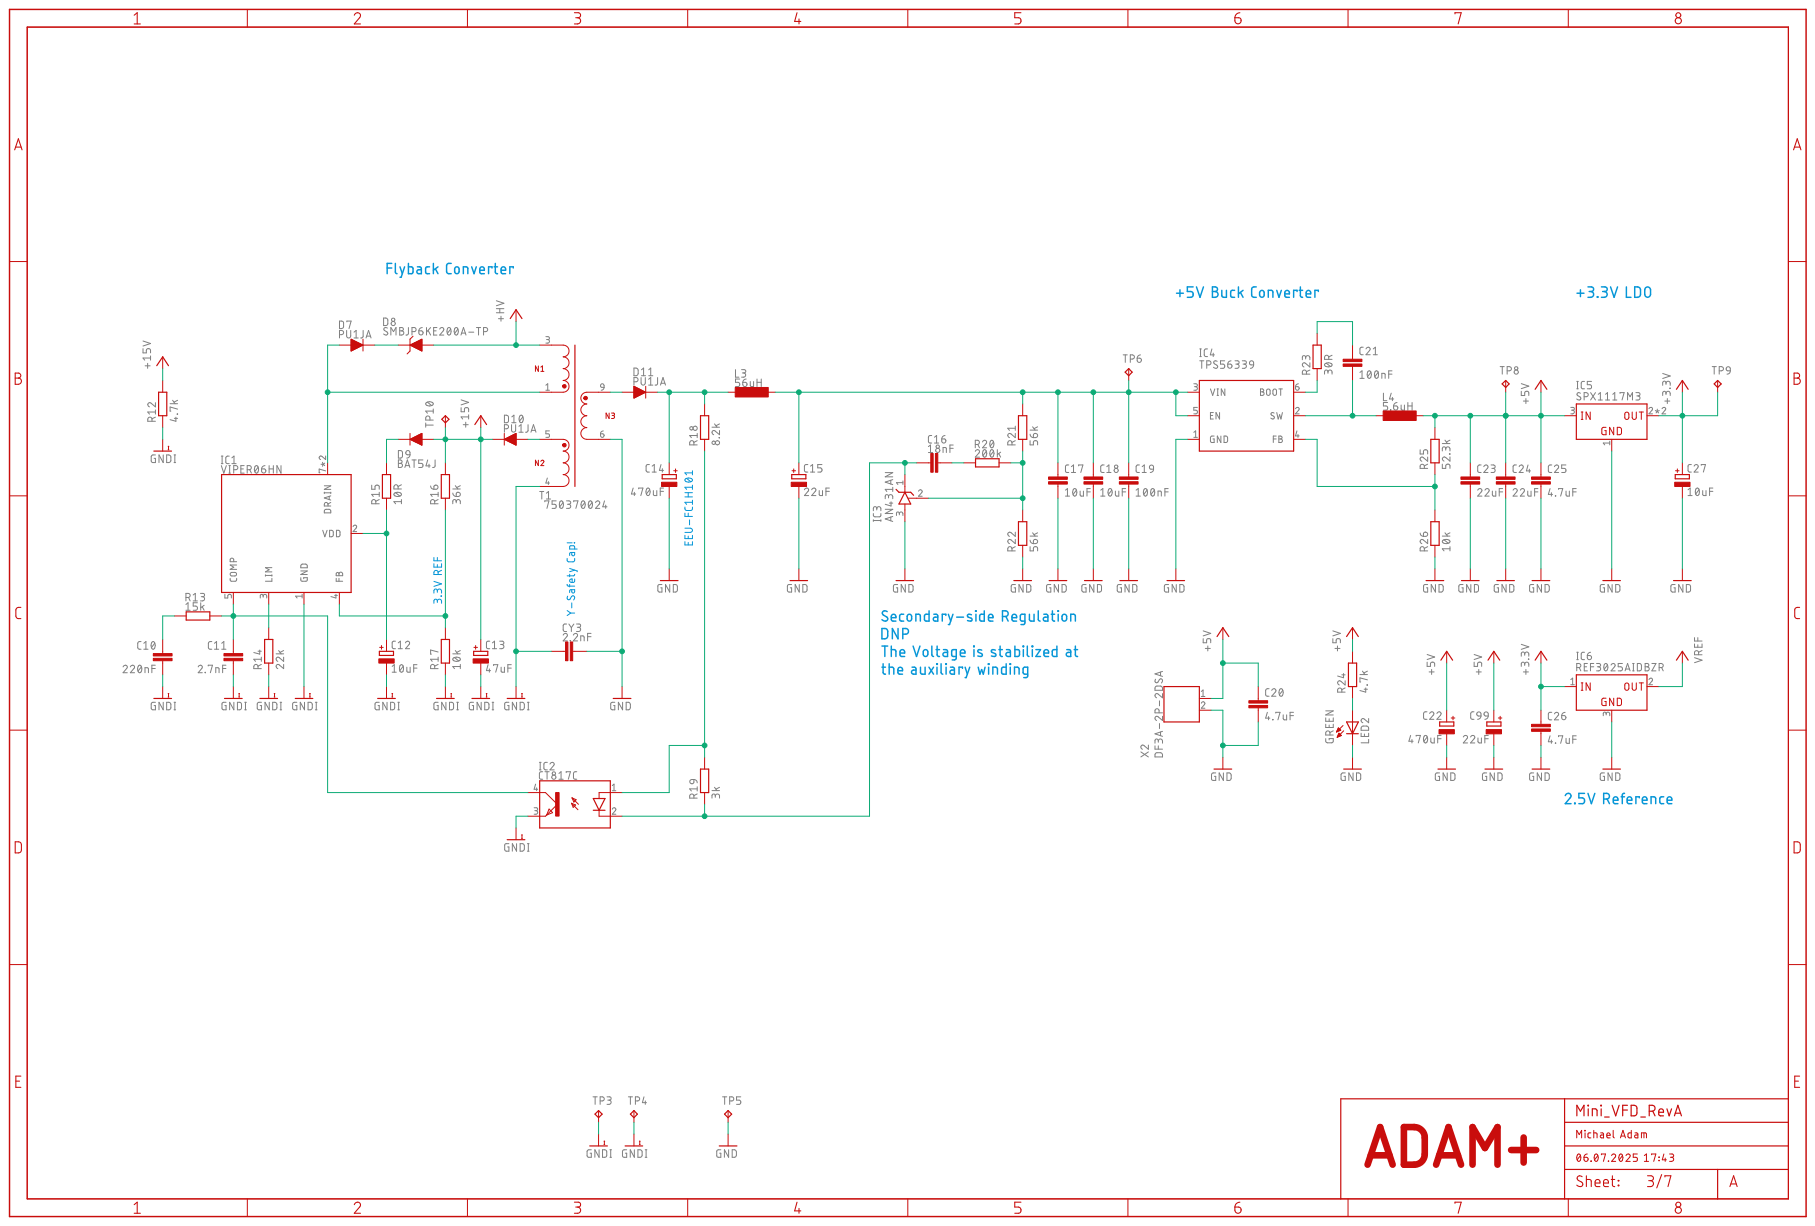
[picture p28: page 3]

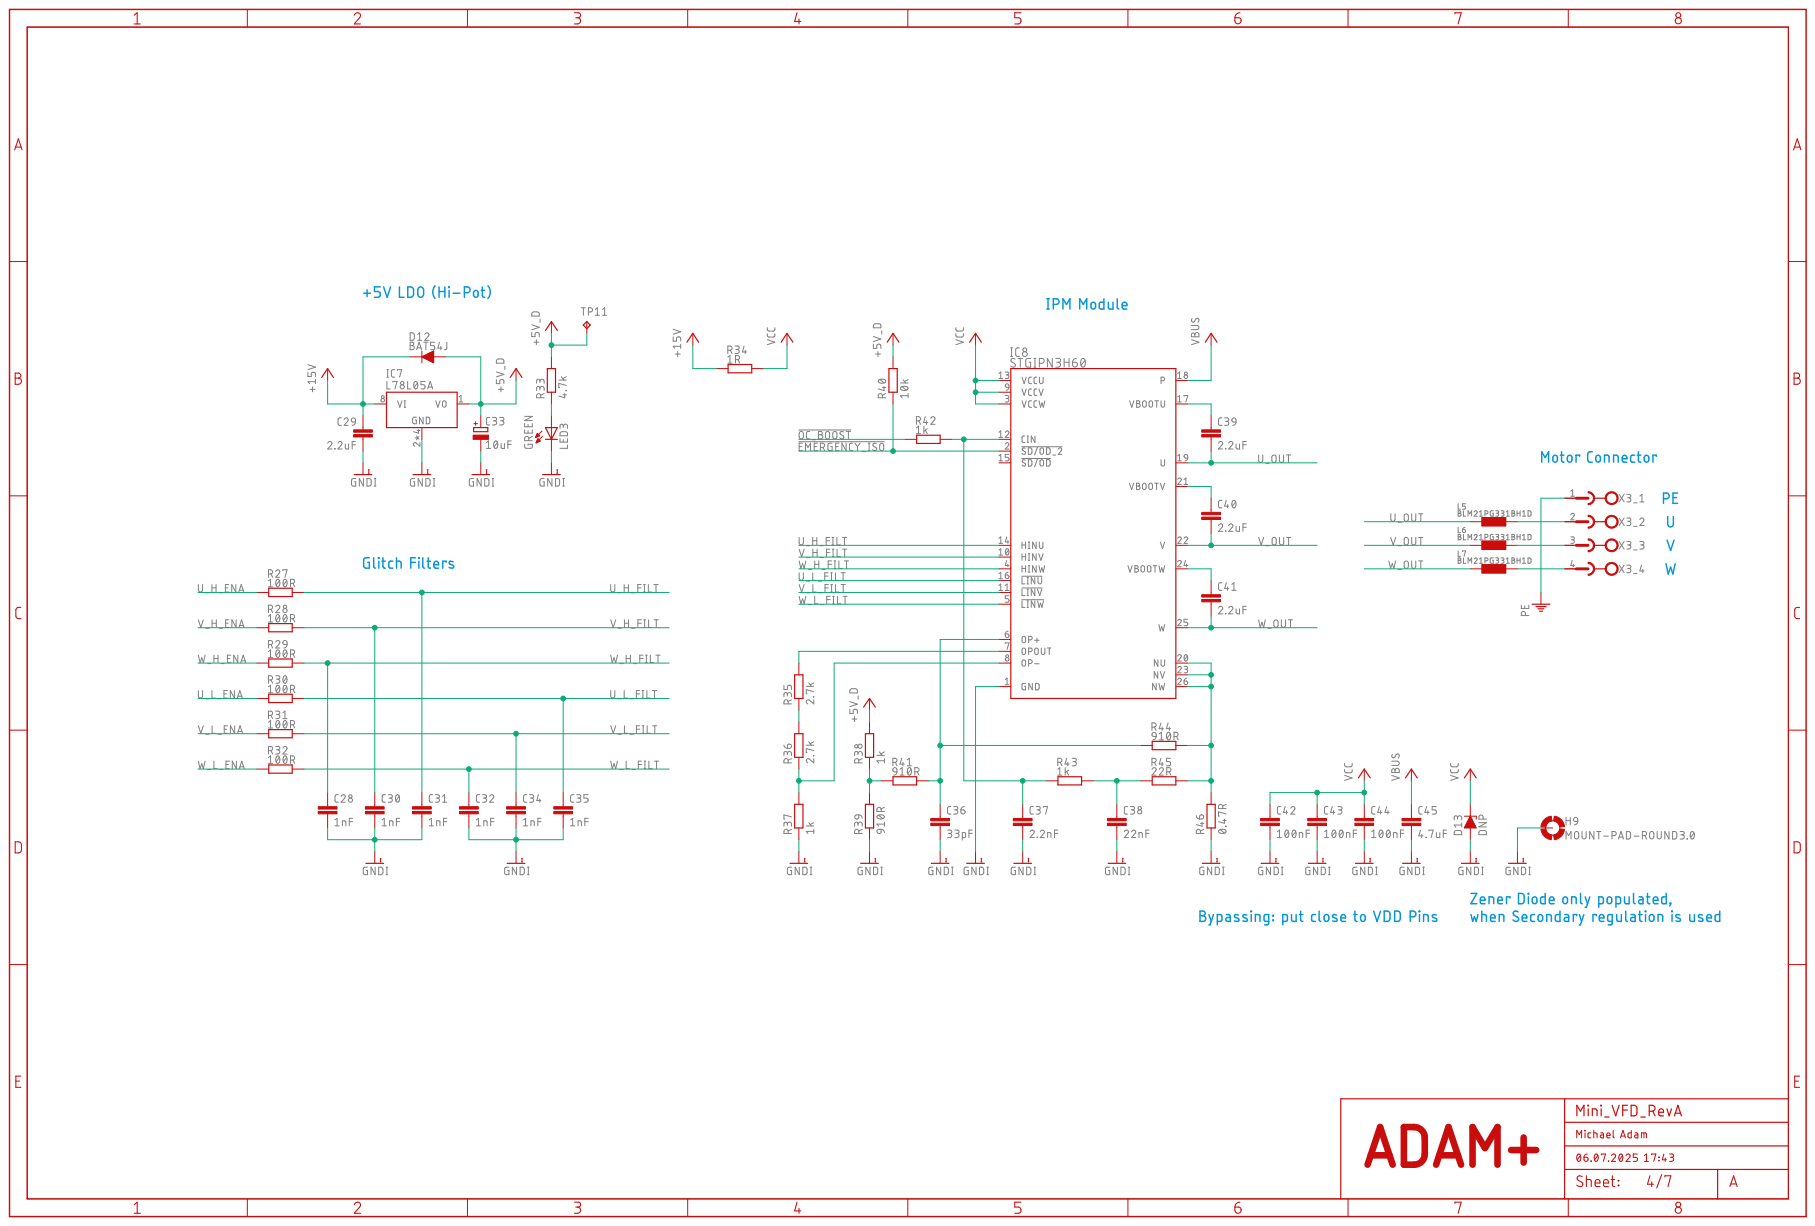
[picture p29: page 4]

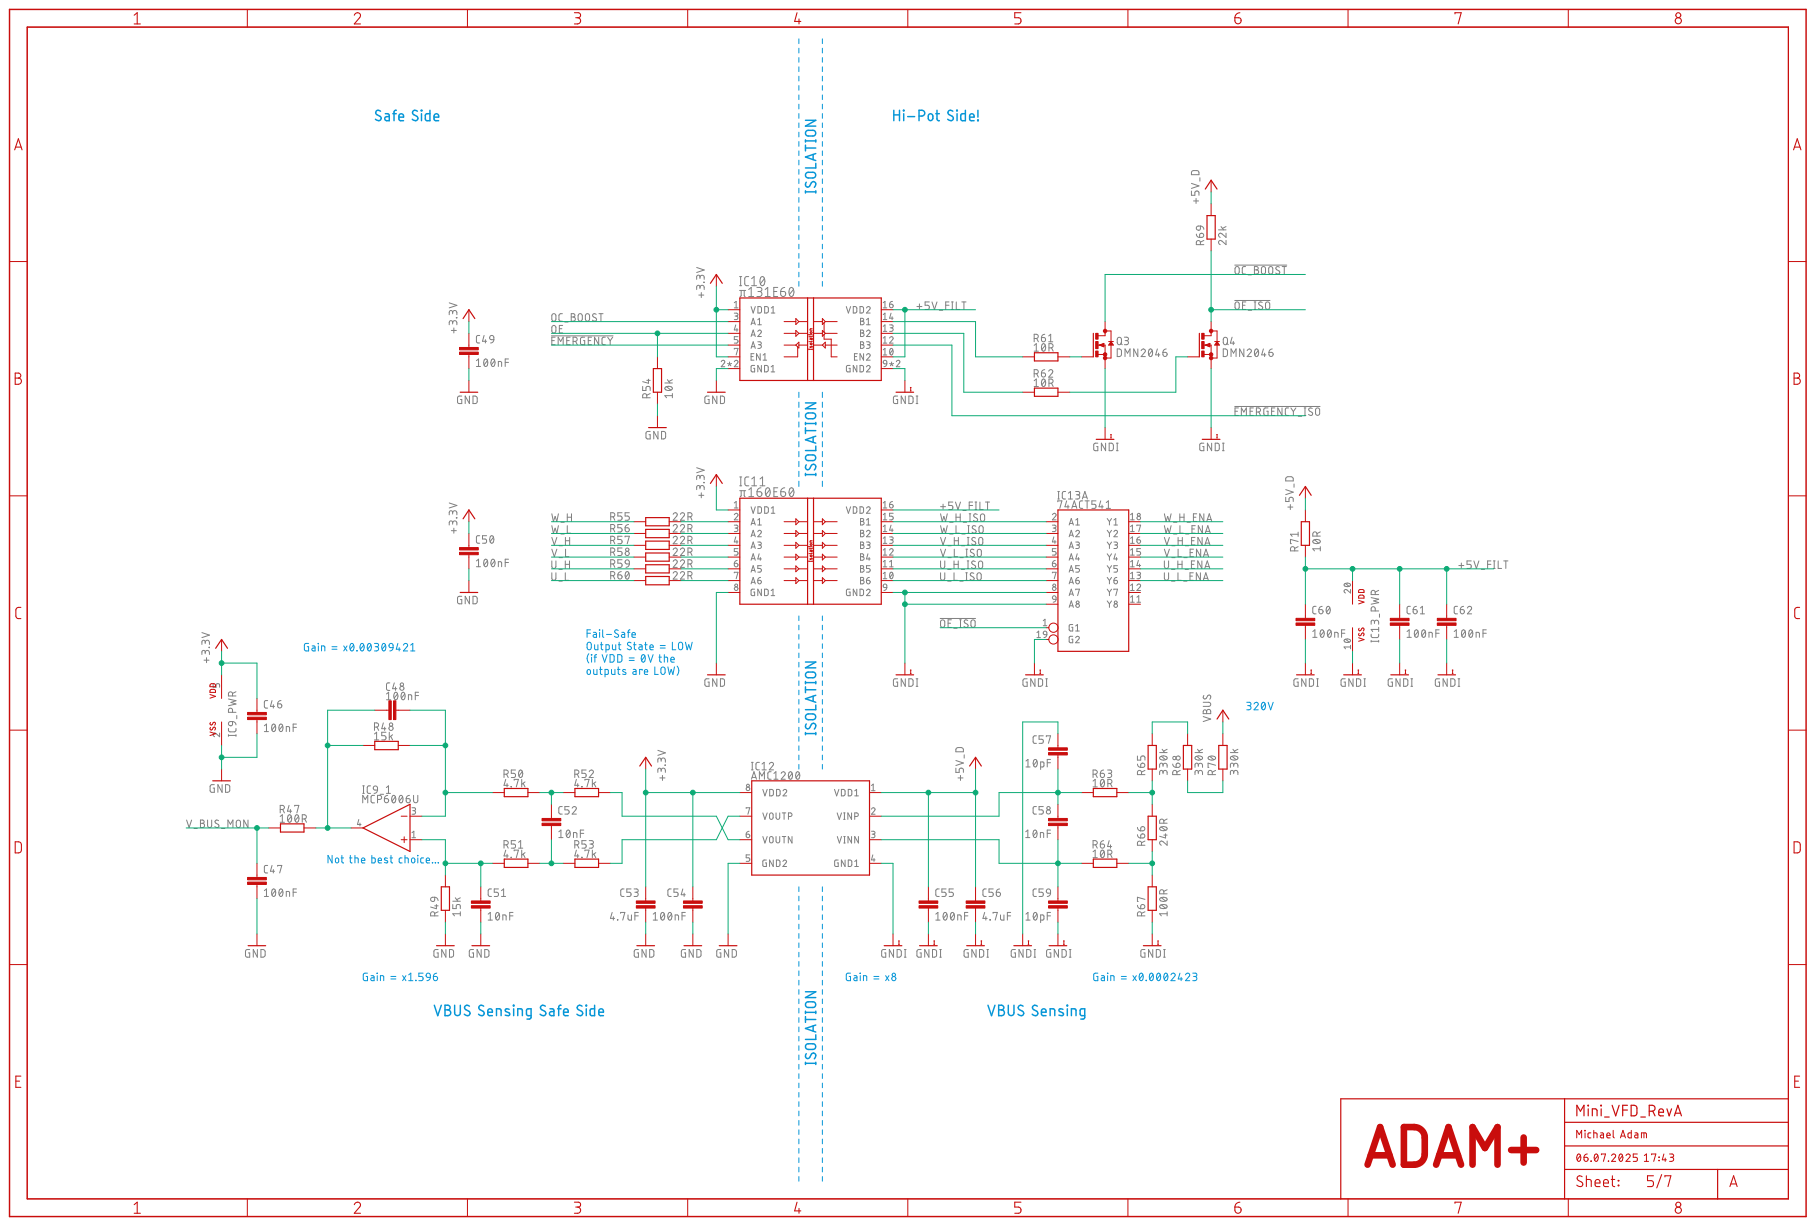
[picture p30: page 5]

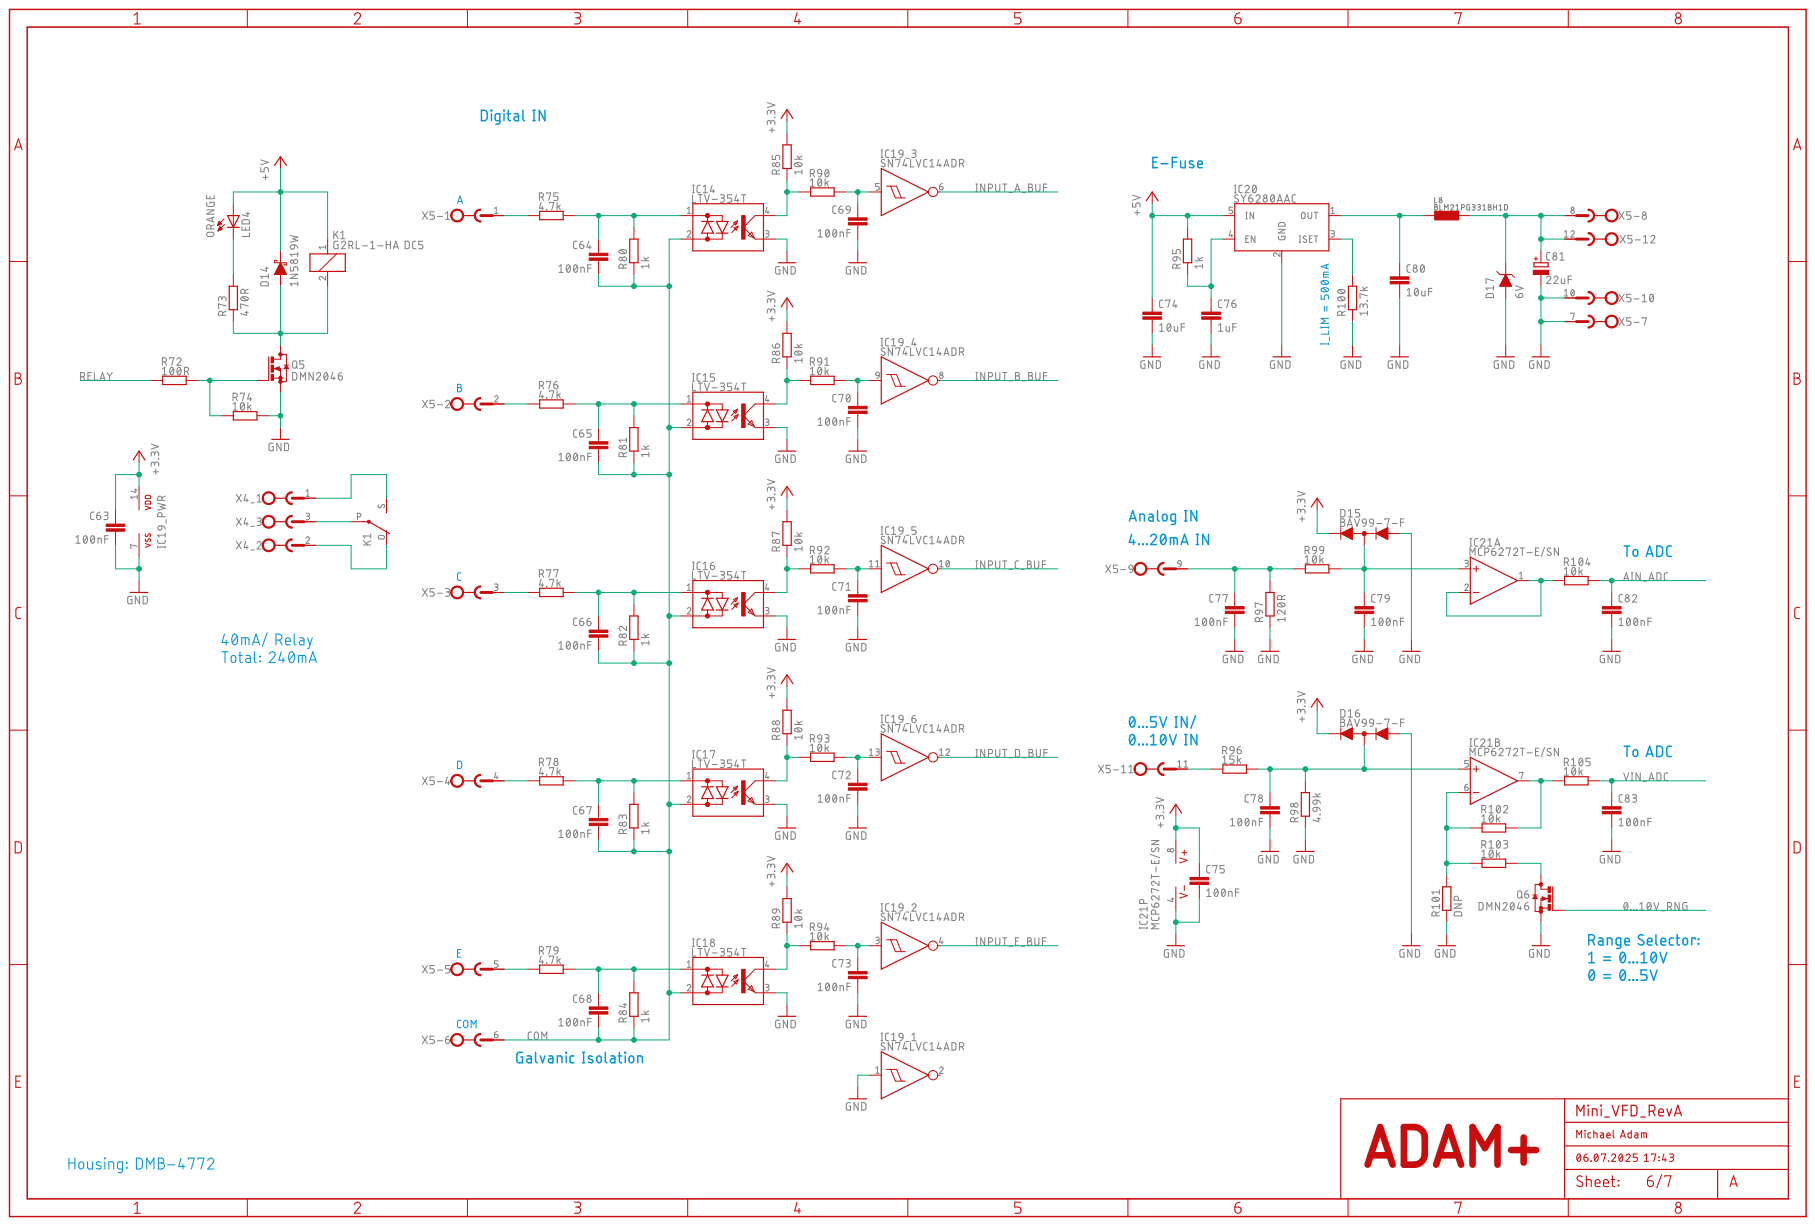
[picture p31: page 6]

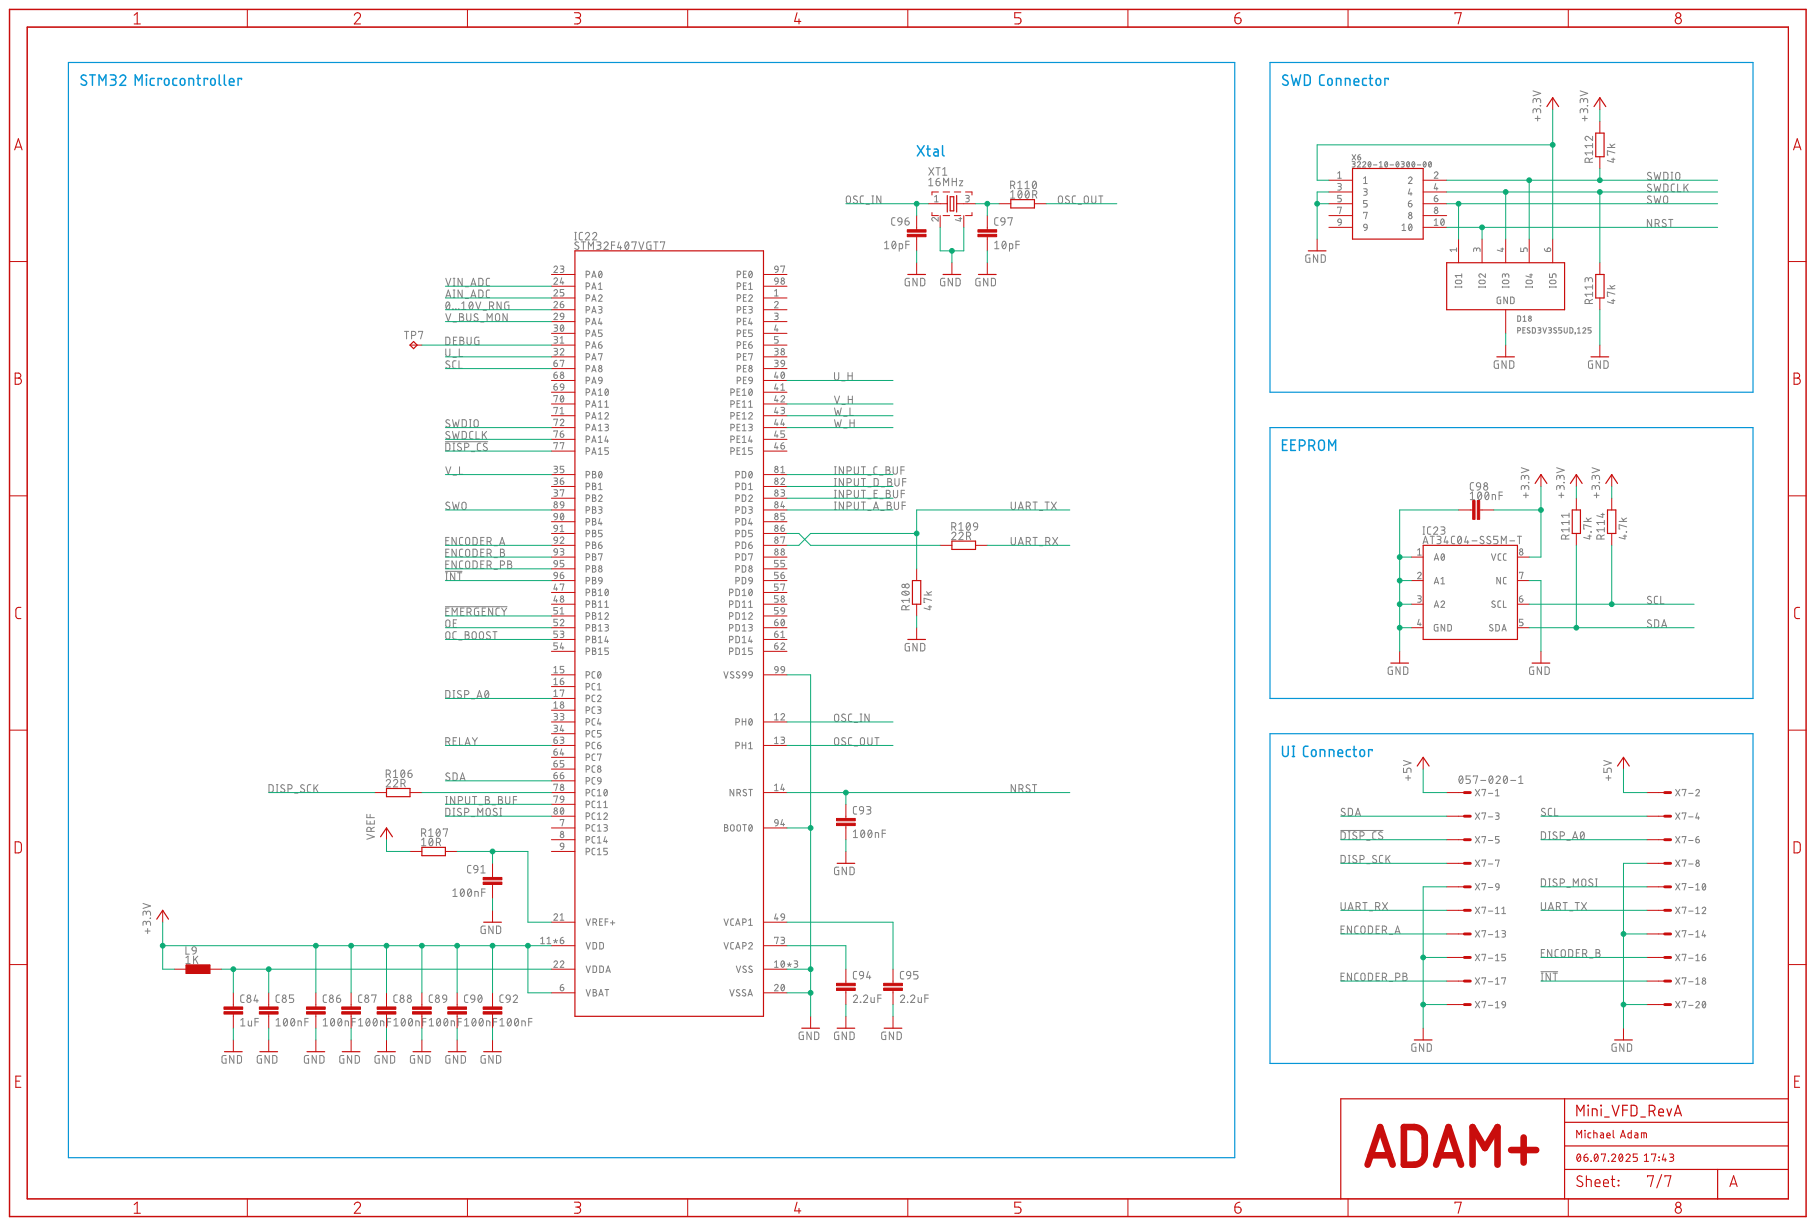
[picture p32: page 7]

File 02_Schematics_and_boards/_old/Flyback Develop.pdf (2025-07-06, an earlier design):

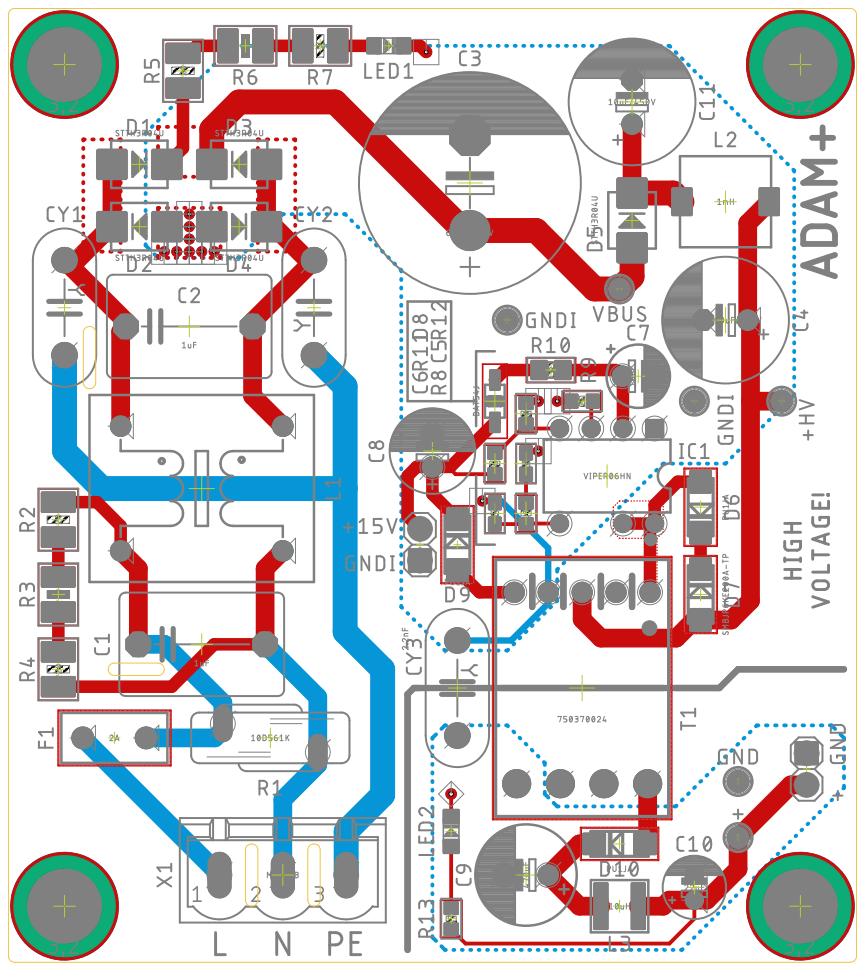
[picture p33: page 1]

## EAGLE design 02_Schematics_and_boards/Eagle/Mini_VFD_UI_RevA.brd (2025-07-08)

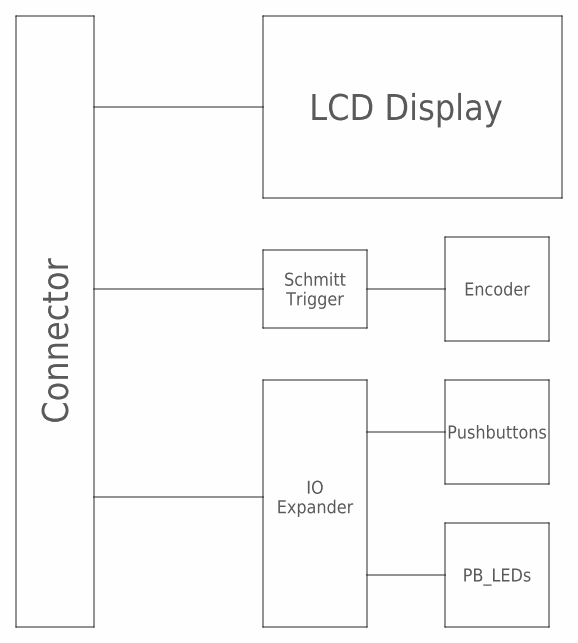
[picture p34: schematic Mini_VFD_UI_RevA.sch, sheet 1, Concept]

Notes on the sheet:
LCD Display
Connector
Encoder
IO Expander
Pushbuttons
PB_LEDs
Schmitt Trigger

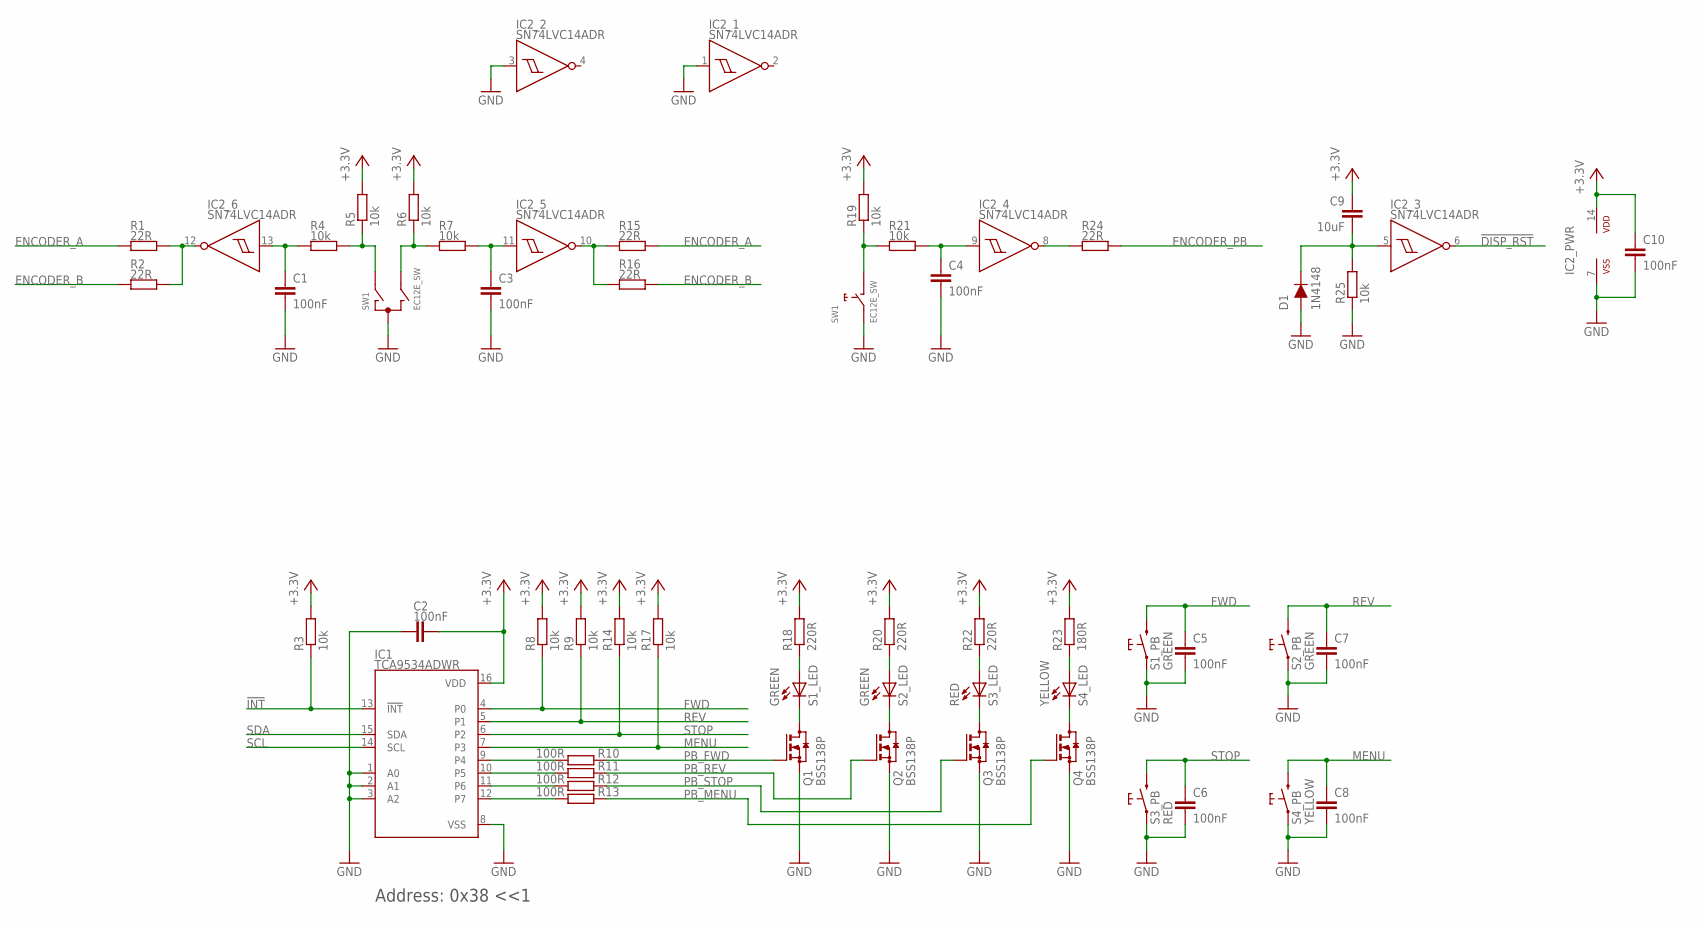
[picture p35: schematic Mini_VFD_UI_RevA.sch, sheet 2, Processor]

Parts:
C1, C2, C3, C4, C5, C6, C7, C8, C10: 100nF; C0603
C9: 10uF; C1206
D1: 1N4148; SOD123
IC1: TCA9534ADWR; SOIC16R
IC2: SN74LVC14ADR; SO14
Q1, Q2, Q3, Q4: BSS138P; SOT23
R1, R2, R15, R16, R24: 22R; R0603
R3, R4, R5, R6, R7, R8, R9, R14, R17, R19, R21, R25: 10k; R0603
R10, R11, R12, R13: 100R; R0603
R18, R20, R22: 220R; R0603
R23: 180R; R0603
S1, S2: GREEN; PB_ALIEXPRESS
S3: RED; PB_ALIEXPRESS
S4: YELLOW; PB_ALIEXPRESS
SW1: EC12E_SW; ALPS_EC12E_SW

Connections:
!DISP_RST: IC2.6 (O); also elsewhere on the board
!INT: IC1.13 (!INT), R3.1; also elsewhere on the board
+3.3V: C2.2, C9.1, C10.1, IC1.16 (VDD), IC2.14 (VDD), R3.2, R5.2, R6.2, R8.2, R9.2, R14.2, R17.2, R18.2, R19.2, R20.2, R22.2, R23.2; also elsewhere on the board
ENCODER_A: R1.1, R15.2; also elsewhere on the board
ENCODER_B: R2.1, R16.2; also elsewhere on the board
ENCODER_PB: R24.2; also elsewhere on the board
FWD: C5.1, IC1.4 (P0), R8.1, S1.2A (2), S1.2B (2)
GND: C1.2, C2.1, C3.2, C4.2, C5.2, C6.2, C7.2, C8.2, C10.2, D1.2 (A), IC1.1 (A0), IC1.2 (A1), IC1.3 (A2), IC1.8 (VSS), IC2.1 (I), IC2.3 (I), IC2.7 (VSS), Q1.2 (S), Q2.2 (S), Q3.2 (S), Q4.2 (S), R25.1, S1.1A (1), S1.1B (1), S2.1A (1), S2.1B (1), S3.1A (1), S3.1B (1), S4.1A (1), S4.1B (1), SW1.C, SW1.E (2); also elsewhere on the board
MENU: C8.1, IC1.7 (P3), R17.1, S4.2A (2), S4.2B (2)
unnamed: R4.2, R5.1, SW1.A
unnamed: R6.1, R7.1, SW1.B
unnamed: C1.1, IC2.13 (I), R4.1
unnamed: C3.1, IC2.11 (I), R7.2
unnamed: R19.1, R21.1, SW1.D (1)
unnamed: C4.1, IC2.9 (I), R21.2
unnamed: IC2.10 (O), R15.1, R16.1
unnamed: IC2.12 (O), R1.2, R2.2
unnamed: C9.2, D1.1 (C), IC2.5 (I), R25.2
unnamed: IC1.12 (P7), R13.1
unnamed: IC1.11 (P6), R12.1
unnamed: IC1.10 (P5), R11.1
unnamed: IC1.9 (P4), R10.1
unnamed: Q1.3 (D), S1.- (C)
unnamed: Q2.3 (D), S2.- (C)
unnamed: Q3.3 (D), S3.- (C)
unnamed: Q4.3 (D), S4.- (C)
unnamed: R18.1, S1.+ (A)
unnamed: R20.1, S2.+ (A)
unnamed: R22.1, S3.+ (A)
unnamed: R23.1, S4.+ (A)
unnamed: IC2.8 (O), R24.1
PB_FWD: Q1.1 (G), R10.2
PB_MENU: Q4.1 (G), R13.2
PB_REV: Q2.1 (G), R11.2
PB_STOP: Q3.1 (G), R12.2
REV: C7.1, IC1.5 (P1), R9.1, S2.2A (2), S2.2B (2)
SCL: IC1.14 (SCL); also elsewhere on the board
SDA: IC1.15 (SDA); also elsewhere on the board
STOP: C6.1, IC1.6 (P2), R14.1, S3.2A (2), S3.2B (2)

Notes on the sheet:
Address: 0x38 <<1

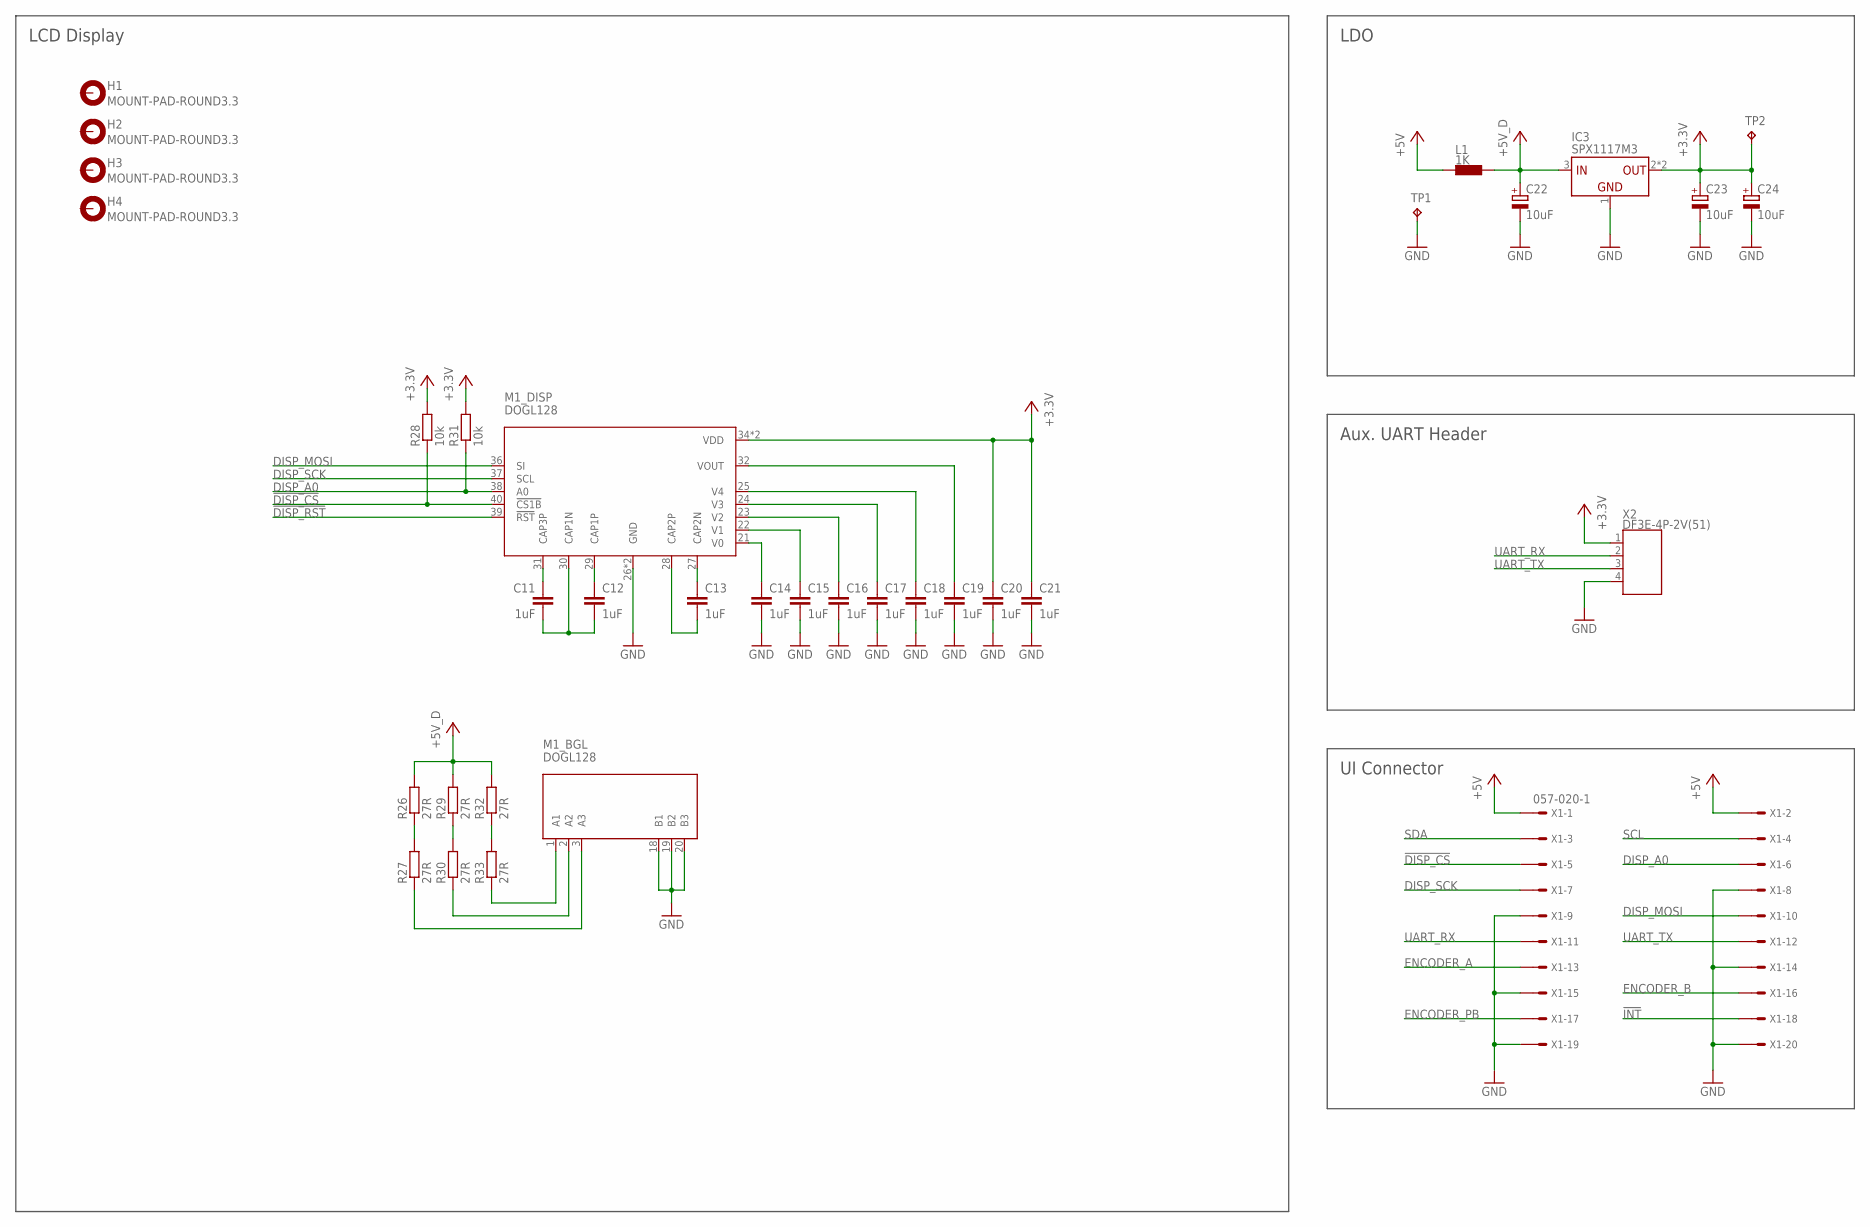
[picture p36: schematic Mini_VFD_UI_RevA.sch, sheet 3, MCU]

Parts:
C11, C12, C13, C14, C15, C16, C17, C18, C19, C20, C21: 1uF; C0603
C22, C23, C24: 10uF; CT3528
H1, H2, H3, H4: MOUNT-PAD-ROUND3.3; 3,3-PAD
IC3: SPX1117M3; SOT223
L1: 1K; R0603
M1: DOGL128; DOGL128-6
R26, R27, R29, R30, R32, R33: 27R; R1206
R28, R31: 10k; R0603
TP1, TP2: TPTP10R; TP10R
X1: 057-020-1
X2: DF3E-4P-2V(51); DF3E-4P-2V

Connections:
!DISP_CS: M1.40 (!CS1B), R28.1, X1.5
!DISP_RST: M1.39 (!RST); also elsewhere on the board
!INT: X1.18; also elsewhere on the board
+3.3V: C20.1, C21.1, C23.+, C24.+, IC3.2 (VOUT), IC3.4 (VOUT), M1.34 (VDD), M1.35 (VDD), R28.2, R31.2, TP2.TP, X2.1; also elsewhere on the board
+5V: L1.2, X1.1, X1.2
+5V_D: C22.+, IC3.3 (VIN), L1.1, R26.2, R29.2, R32.2
DISP_A0: M1.38 (A0), R31.1, X1.6
DISP_MOSI: M1.36 (SI), X1.10
DISP_SCK: M1.37 (SCL), X1.7
ENCODER_A: X1.13; also elsewhere on the board
ENCODER_B: X1.16; also elsewhere on the board
ENCODER_PB: X1.17; also elsewhere on the board
GND: C14.2, C15.2, C16.2, C17.2, C18.2, C19.2, C20.2, C21.2, C22.-, C23.-, C24.-, IC3.1 (GND), M1.18 (B1), M1.19 (B2), M1.20 (B3), M1.26 (GND), M1.33 (GND), TP1.TP, X1.8, X1.9, X1.14, X1.15, X1.19, X1.20, X2.4; also elsewhere on the board
unnamed: C13.2, M1.28 (CAP2P)
unnamed: C13.1, M1.27 (CAP2N)
unnamed: C12.1, M1.29 (CAP1P)
unnamed: C11.2, C12.2, M1.30 (CAP1N)
unnamed: C11.1, M1.31 (CAP3P)
unnamed: C14.1, M1.21 (V0)
unnamed: C15.1, M1.22 (V1)
unnamed: C16.1, M1.23 (V2)
unnamed: C17.1, M1.24 (V3)
unnamed: C18.1, M1.25 (V4)
unnamed: C19.1, M1.32 (VOUT)
unnamed: R26.1, R27.2
unnamed: M1.3 (A3), R27.1
unnamed: M1.2 (A2), R30.1
unnamed: M1.1 (A1), R33.1
unnamed: R29.1, R30.2
unnamed: R32.1, R33.2
SCL: X1.4; also elsewhere on the board
SDA: X1.3; also elsewhere on the board
UART_RX: X1.11, X2.2
UART_TX: X1.12, X2.3

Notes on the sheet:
LDO
LCD Display
UI Connector
Aux. UART Header

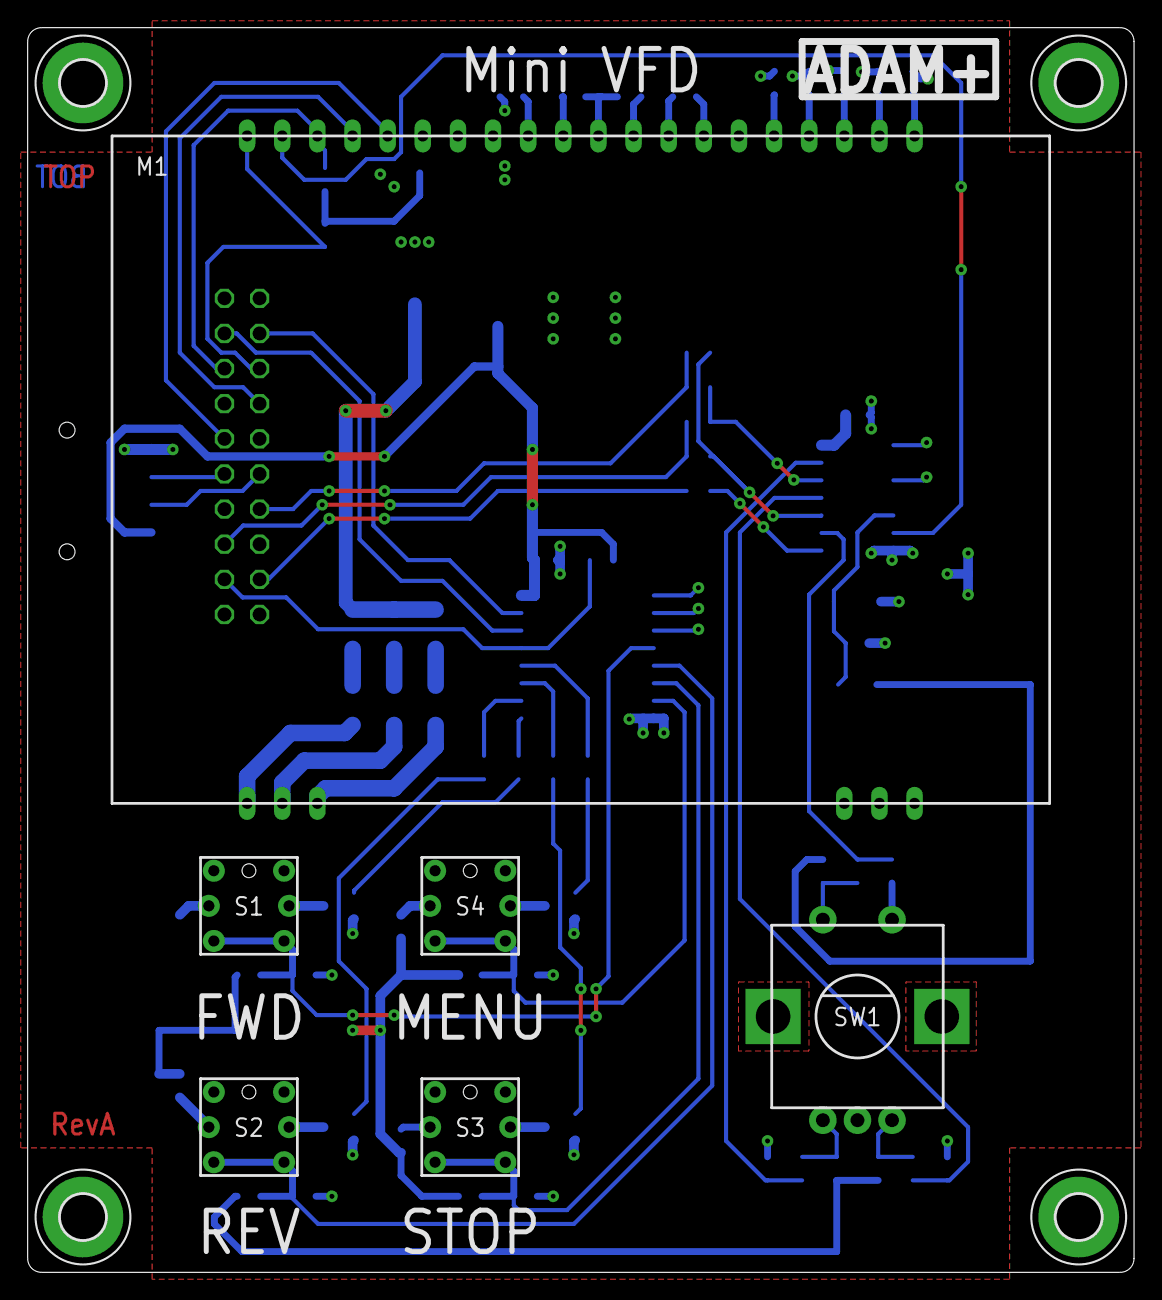
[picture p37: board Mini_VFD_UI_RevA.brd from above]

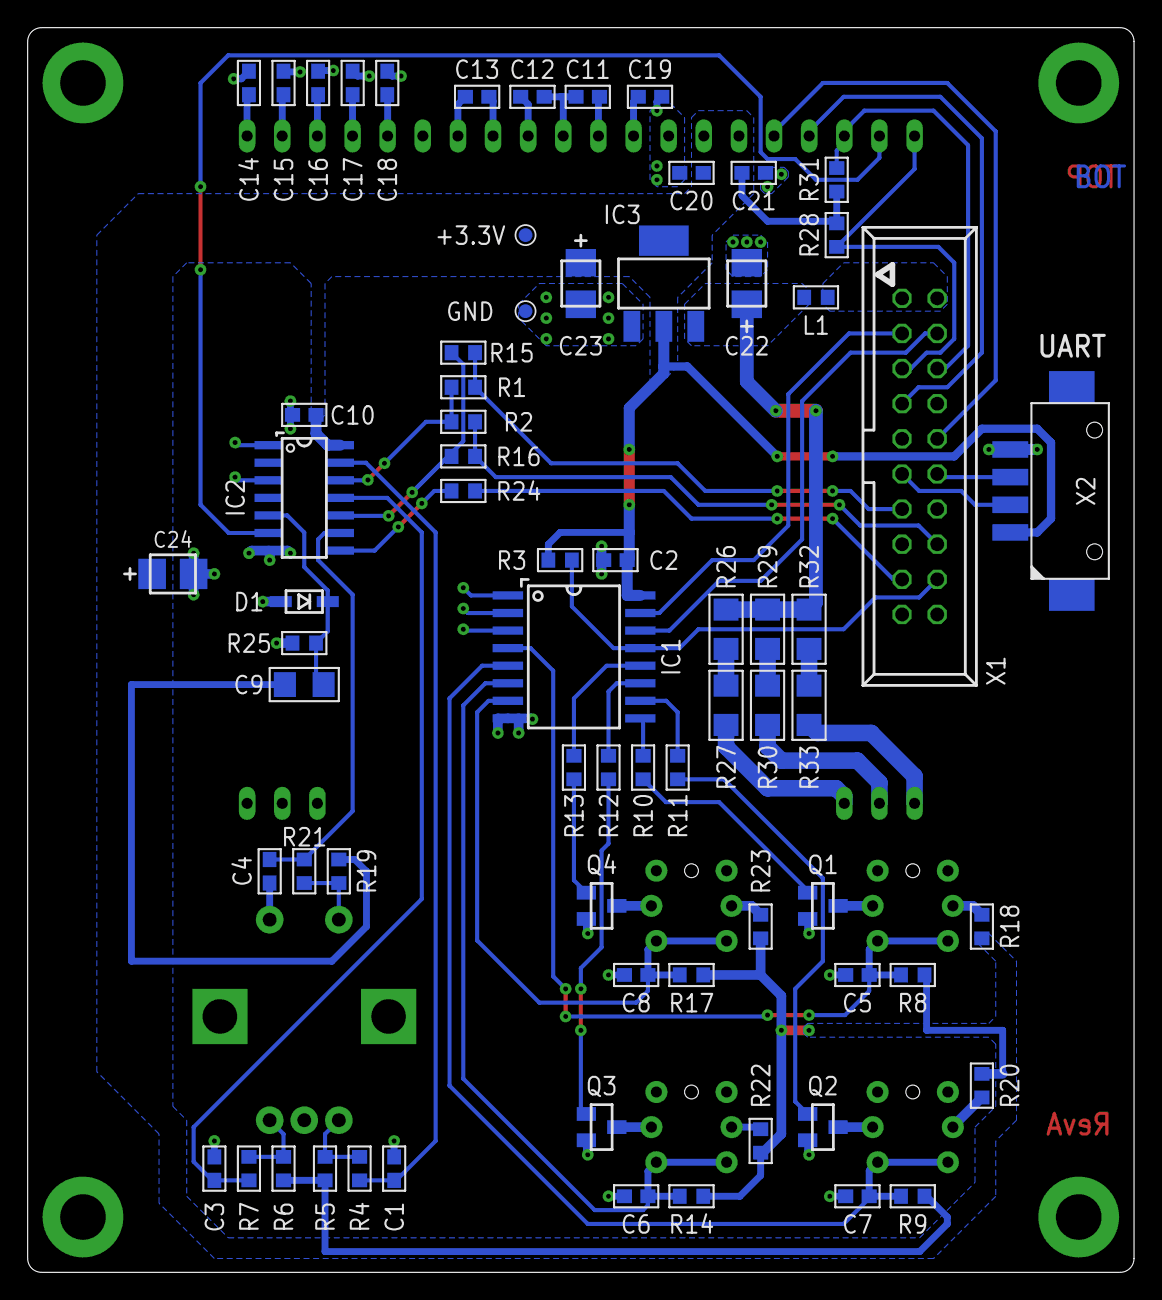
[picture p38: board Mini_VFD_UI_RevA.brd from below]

Board: 2 copper layers, 80.0 x 90.0 mm, 80 parts (70 on the bottom side), 64 nets.

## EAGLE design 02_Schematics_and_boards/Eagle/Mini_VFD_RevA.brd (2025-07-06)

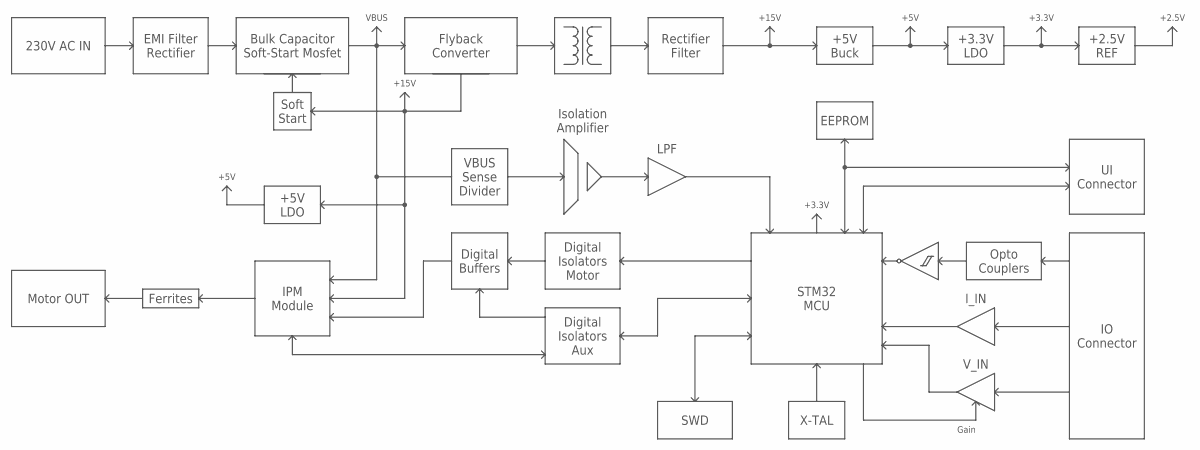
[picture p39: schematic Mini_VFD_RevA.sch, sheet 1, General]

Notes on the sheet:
230V AC IN
EMI Filter Rectifier
Bulk Capacitor Soft-Start Mosfet
Soft Start
Flyback Converter
Rectifier Filter
VBUS
+15V
IPM Module
+5V Buck
+3.3V LDO
+5V
+3.3V
Motor OUT
Ferrites
Digital Isolators Motor
STM32 MCU
Opto Couplers
IO Connector
X-TAL
SWD
Digital Buffers
Digital Isolators Aux
+2.5V REF
+2.5V
VBUS Sense Divider
Isolation Amplifier
LPF
I_IN
V_IN
Gain
EEPROM
UI Connector
+5V LDO

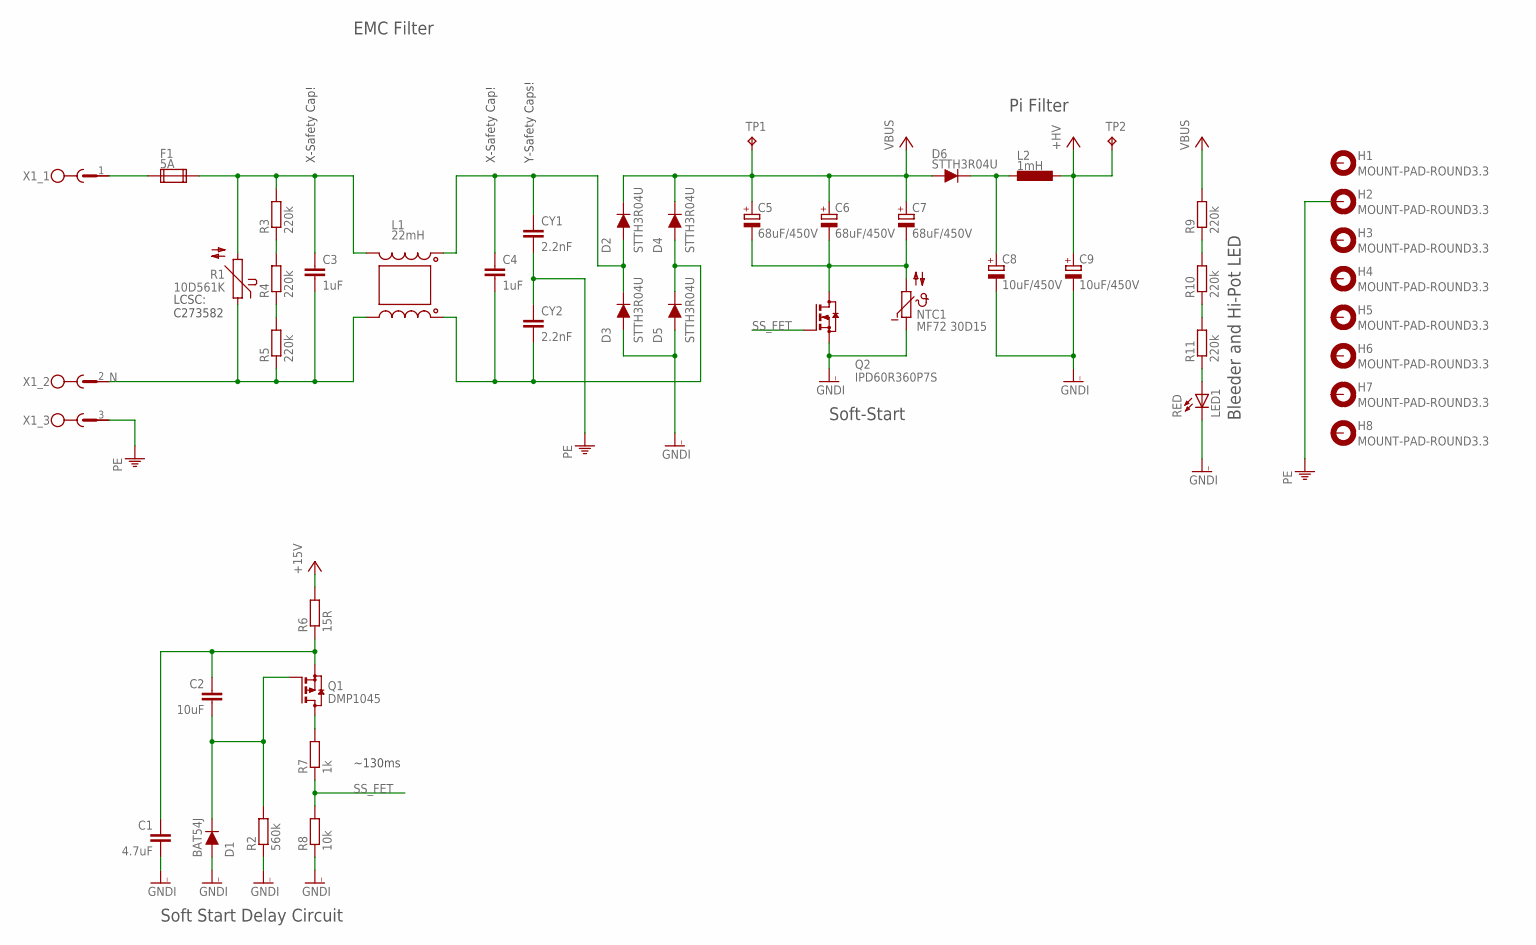
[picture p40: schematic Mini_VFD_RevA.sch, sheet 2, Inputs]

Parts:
C1: 4.7uF; C0805
C2: 10uF; C0805
C3, C4: 1uF; C102-082X133
C5, C6, C7: 68uF/450V; E7,5-18
C8, C9: 10uF/450V; E5-10,5
CY1, CY2: 2.2nF; YC7B5
D1: BAT54J; SOD123
D2, D3, D4, D5, D6: STTH3R04U; SMB
F1: 5A; SH25
H1, H2, H3, H4, H5, H6, H7, H8: MOUNT-PAD-ROUND3.3; 3,3-PAD
L1: 22mH; CMC_PDMCAT18107
L2: 1mH; SLH0704
LED1: RED; LED_0805
NTC1: MF72 30D15; MF72
Q1: DMP1045; SOT23
Q2: IPD60R360P7S; TO252
R1: 10D561K; S10K175
R2: 560k; R0603
R3, R4, R5, R9, R10, R11: 220k; R1206
R6: 15R; 0207/10
R7: 1k; R0603
R8: 10k; R0603
TP1, TP2: TPTP10R; TP10R
X1: MSTBV3

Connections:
+15V: R6.2; also elsewhere on the board
+HV: C9.+, L2.1, TP2.TP; also elsewhere on the board
C_NEG: C5.-, C6.-, C7.-, NTC1.2, Q2.3 (D)
GNDI: C1.2, C8.-, C9.-, D1.2 (A), D3.A, D5.A, LED1.C, NTC1.1, Q2.2 (S), R2.1, R8.1; also elsewhere on the board
L: F1.1, X1.1
L_FILT: C4.1, CY1.1, D2.A, D3.C, L1.IN1
L_FUSED: C3.1, F1.2, L1.OUT1, R1.2, R3.2
N: C3.2, L1.OUT2, R1.1, R5.1, X1.2
unnamed: Q1.3 (D), R7.2
unnamed: C2.2, D1.1 (C), Q1.1 (G), R2.2
unnamed: C1.1, C2.1, Q1.2 (S), R6.1
unnamed: R3.1, R4.2
unnamed: R4.1, R5.2
unnamed: R9.1, R10.2
unnamed: R10.1, R11.2
unnamed: LED1.A, R11.1
N_FILT: C4.2, CY2.2, D4.A, D5.C, L1.IN2
PE: CY1.2, CY2.1, H2.B3,3, X1.3; also elsewhere on the board
SS_FET: Q2.1 (G), R7.1, R8.2
VBUS: C5.+, C6.+, C7.+, D2.C, D4.C, D6.A, R9.2, TP1.TP; also elsewhere on the board
VBUS_FILT: C8.+, D6.C, L2.2

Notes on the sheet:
LCSC: C273582
X-Safety Cap!
Y-Safety Caps!
Soft-Start
Pi Filter
Bleeder and Hi-Pot LED
Soft Start Delay Circuit
~130ms
EMC Filter

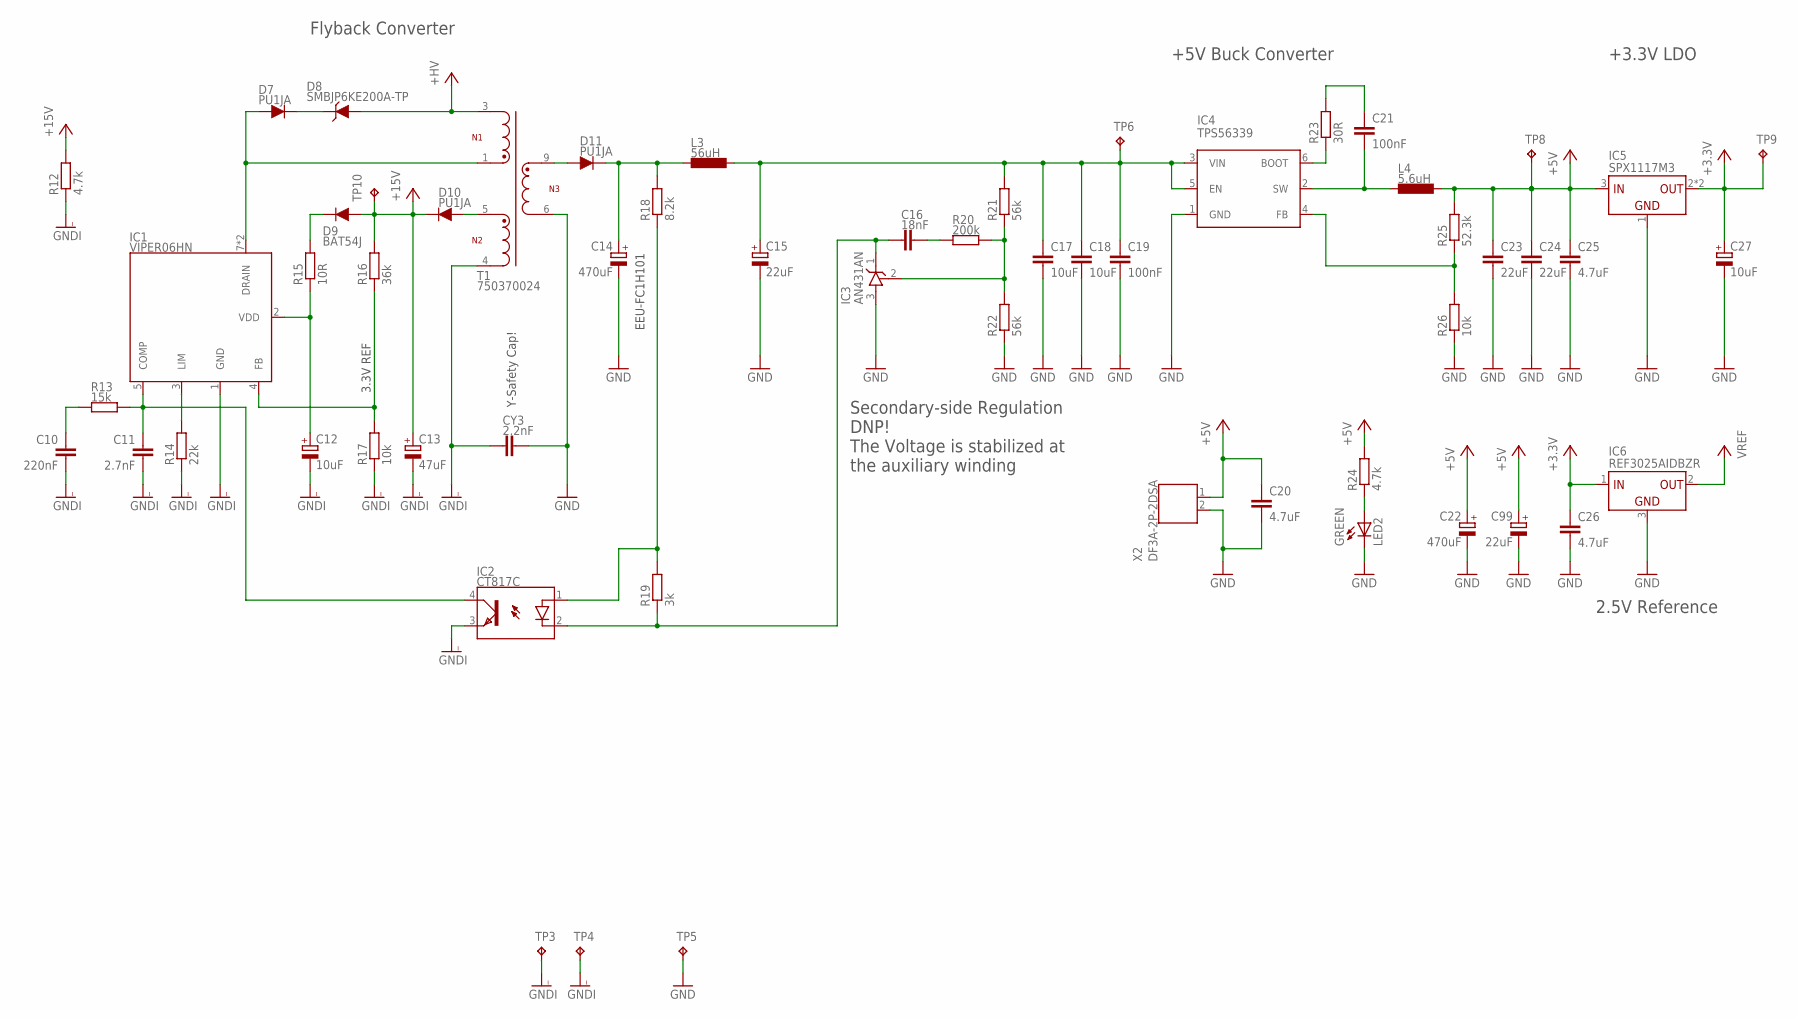
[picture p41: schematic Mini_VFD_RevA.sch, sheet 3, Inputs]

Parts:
C10: 220nF; C0603
C11: 2.7nF; C0603
C12: 10uF; E2,5-5
C13: 47uF; E2,5-7
C14, C22: 470uF; E5-10,5
C15, C99: 22uF; E2-5
C16: 18nF; C0603
C17, C18: 10uF; C1206
C19, C21: 100nF; C0603
C20: 4.7uF; C0805
C23, C24: 22uF; C1206
C25, C26: 4.7uF; C0603
C27: 10uF; CT3528
CY3: 2.2nF; YC7B5
D7, D10, D11: PU1JA; DO214AC
D8: SMBJP6KE200A-TP; SMB
D9: BAT54J; SOD123
IC1: VIPER06HN; DIL07
IC2: CT817C; SMD4
IC3: AN431AN; SOT23
IC4: TPS56339; TSOT23-6
IC5: SPX1117M3; SOT223
IC6: REF3025AIDBZR; SOT23
L3: 56uH; PDPTAT
L4: 5.6uH; DH0530H
LED2: GREEN; LED_0805
R12: 4.7k; R1206
R13: 15k; R0603
R14: 22k; R0603
R15: 10R; R0805
R16: 36k; R0603
R17, R26: 10k; R0603
R18: 8.2k; R0603
R19: 3k; R0603
R20: 200k; R0603
R21, R22: 56k; R0603
R23: 30R; R0603
R24: 4.7k; R0603
R25: 52.3k; R0603
T1: 750370024; WE-OLSTM_EE13_L13.72W20.45H10.8
TP3, TP4, TP5, TP6, TP8, TP9, TP10: TP_SOLDREYE; SOLDER_EYE
X2: DF3A-2P-2DSA

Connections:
+3.3V: C26.1, C27.+, IC5.2 (VOUT), IC5.4 (VOUT), IC6.1 (VIN), TP9.1; also elsewhere on the board
+5V: C20.1, C22.+, C23.1, C24.1, C25.1, C99.+, IC5.3 (VIN), L4.P$1 (1), R24.2, R25.2, TP8.1, X2.1; also elsewhere on the board
+15V: C13.+, D9.2 (A), D10.C, R12.2, R16.2, TP10.1; also elsewhere on the board
+HV: D8.A, T1.3; also elsewhere on the board
AUX_OUT: D10.A, T1.5
BOOT_+5V: IC4.6 (BOOT), R23.1
D: D7.A, IC1.7 (DRAIN), IC1.8 (DRAIN), T1.1
FB: IC4.4 (FB), R25.1, R26.2
GND: C14.-, C15.-, C17.2, C18.2, C19.2, C20.2, C22.-, C23.2, C24.2, C25.2, C26.2, C27.-, C99.-, CY3.2, IC3.3 (A), IC4.1 (GND), IC5.1 (GND), IC6.3 (GND), LED2.C, R22.1, R26.1, T1.6, TP5.1, X2.2; also elsewhere on the board
GNDI: C10.2, C11.2, C12.-, C13.-, CY3.1, IC1.1 (GND), IC2.3 (EMIT), R12.1, R14.1, R17.1, T1.4, TP3.1, TP4.1; also elsewhere on the board
unnamed: D9.1 (C), R15.2
unnamed: IC1.3 (LIM), R14.2
unnamed: IC1.4 (FB), R16.1, R17.2
unnamed: C10.1, R13.1
unnamed: IC3.2 (R), R20.2, R21.1, R22.2
unnamed: D7.C, D8.C
unnamed: C11.1, IC1.5 (COMP), IC2.4 (COL), R13.2
unnamed: C16.1, IC2.2 (C), IC3.1 (C), R19.1
unnamed: IC2.1 (A), R18.1, R19.2
unnamed: LED2.A, R24.1
unnamed: C16.2, R20.1
unnamed: C21.1, R23.2
SEC_OUT: D11.A, T1.9
SW: C21.2, IC4.2 (SW), L4.P$2 (2)
VDD: C14.+, D11.C, L3.2, R18.2
VDD_FILT: C15.+, C17.1, C18.1, C19.1, IC4.3 (VIN), IC4.5 (EN), L3.1, R21.2, TP6.1
VREF: IC6.2 (VOUT); also elsewhere on the board
V_AUX: C12.+, IC1.2 (VDD), R15.1

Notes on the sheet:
3.3V REF
EEU-FC1H101
+5V Buck Converter
+3.3V LDO
Flyback Converter
Secondary-side Regulation DNP! The Voltage is stabilized at the auxiliary winding
2.5V Reference
Y-Safety Cap!

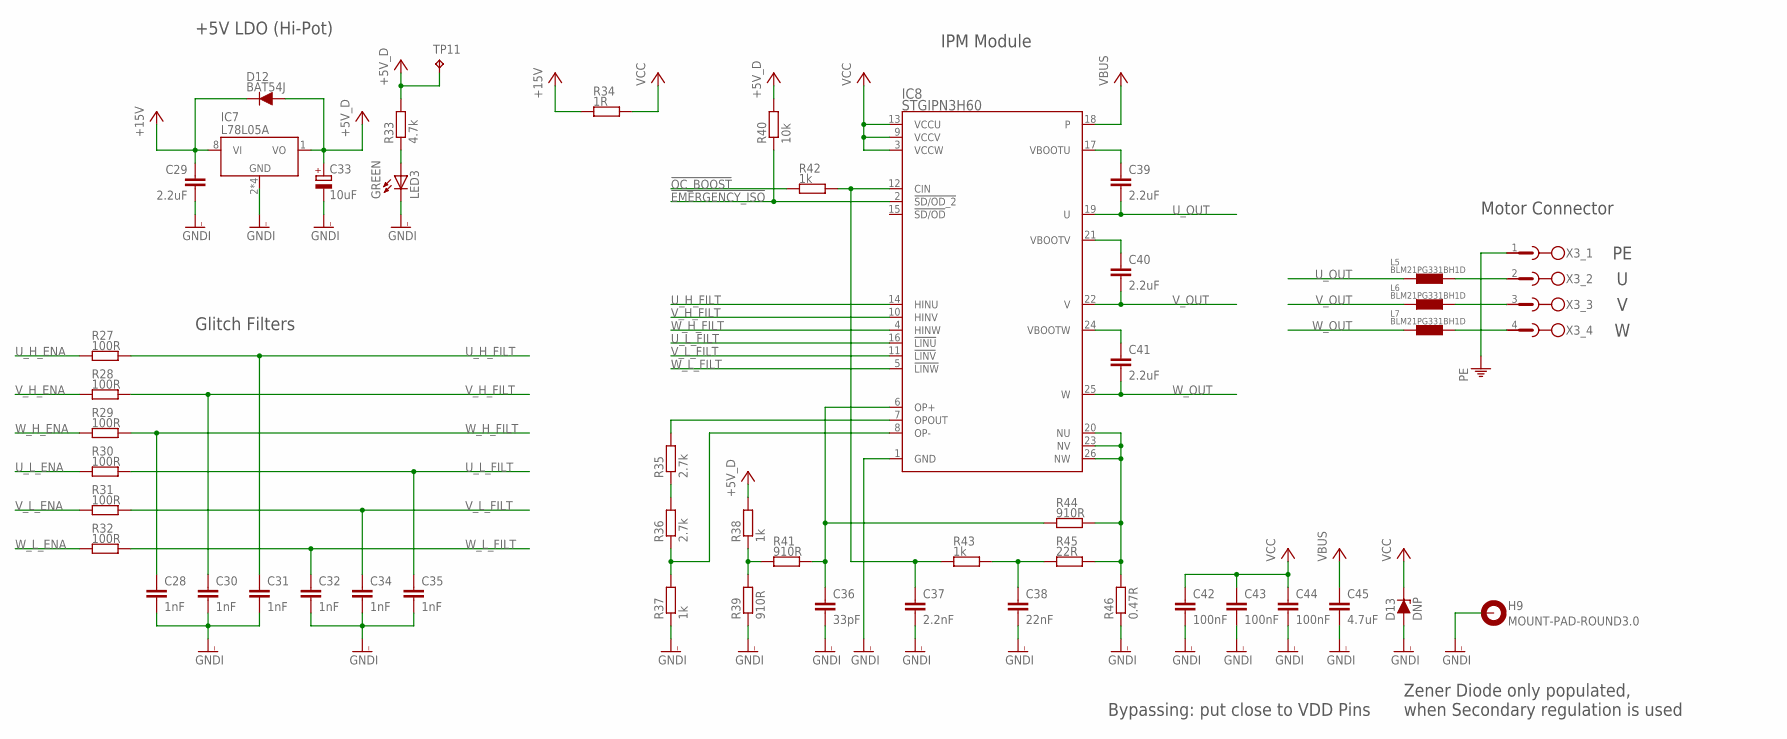
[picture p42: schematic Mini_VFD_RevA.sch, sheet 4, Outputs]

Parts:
C28, C30, C31, C32, C34, C35: 1nF; C0603
C29, C39, C40, C41: 2.2uF; C0805
C33: 10uF; CT3528
C36: 33pF; C0603
C37: 2.2nF; C0603
C38: 22nF; C0603
C42, C43, C44: 100nF; C0603
C45: 4.7uF; C275-126X316
D12: BAT54J; SOD123
D13: DNP; DO214AC
H9: MOUNT-PAD-ROUND3.0; 3,0-PAD
IC7: L78L05A; SOIC8
IC8: STGIPN3H60; NDIP26_12P45X29P25_STM
L5, L6, L7: BLM21PG331BH1D; R0805
LED3: GREEN; LED_0805
R27, R28, R29, R30, R31, R32: 100R; R0603
R33: 4.7k; R0603
R34: 1R; R0805
R35, R36: 2.7k; R0603
R37, R38, R42, R43: 1k; R0603
R39, R41, R44: 910R; R0603
R40: 10k; R0603
R45: 22R; R0603
R46: 0.47R; R2512
TP11: TP_SOLDREYE; SOLDER_EYE
X3: MSTBV4MTSV; MSTBV4

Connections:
!EMERGENCY_ISO: IC8.2 (!SD/OD_2), R40.1; also elsewhere on the board
!OC_BOOST: R42.1; also elsewhere on the board
+5V_D: C33.+, D12.2 (A), IC7.1 (VO), R33.2, R38.2, R40.2, TP11.1; also elsewhere on the board
+15V: C29.1, D12.1 (C), IC7.8 (VI), R34.1; also elsewhere on the board
BOOT_U: C39.1, IC8.17 (VBOOTU)
BOOT_V: C40.1, IC8.21 (VBOOTV)
BOOT_W: C41.1, IC8.24 (VBOOTW)
GNDI: C28.2, C29.2, C30.2, C31.2, C32.2, C33.-, C34.2, C35.2, C36.2, C37.2, C38.2, C42.2, C43.2, C44.2, C45.2, D13.A, H9.B3,0, IC7.2 (GND), IC7.3 (GND), IC7.6 (GND), IC7.7 (GND), IC8.1 (GND), LED3.C, R37.1, R39.1, R46.1; also elsewhere on the board
unnamed: LED3.A, R33.1
unnamed: C38.1, R43.2, R45.1
unnamed: C37.1, IC8.12 (CIN), R42.2, R43.1
unnamed: IC8.8 (OP-), R36.1, R37.2
unnamed: R35.1, R36.2
unnamed: IC8.7 (OPOUT), R35.2
unnamed: R38.1, R39.2, R41.1
unnamed: C36.1, IC8.6 (OP+), R41.2, R44.1
N_COM: IC8.20 (NU), IC8.23 (NV), IC8.26 (NW), R44.2, R45.2, R46.2
PE: X3.1; also elsewhere on the board
U: L5.2, X3.2
U_H_ENA: R27.1; also elsewhere on the board
U_H_FILT: C31.1, IC8.14 (HINU), R27.2
U_L_ENA: R30.1; also elsewhere on the board
U_L_FILT: C35.1, IC8.16 (!LINU), R30.2
U_OUT: C39.2, IC8.19 (U), L5.1
V: L6.2, X3.3
VBUS: C45.1, IC8.18; also elsewhere on the board
VCC: C42.1, C43.1, C44.1, D13.C, IC8.3 (VCCW), IC8.9 (VCCV), IC8.13 (VCCU), R34.2
V_H_ENA: R28.1; also elsewhere on the board
V_H_FILT: C30.1, IC8.10 (HINV), R28.2
V_L_ENA: R31.1; also elsewhere on the board
V_L_FILT: C34.1, IC8.11 (!LINV), R31.2
V_OUT: C40.2, IC8.22 (V), L6.1
W: L7.2, X3.4
W_H_ENA: R29.1; also elsewhere on the board
W_H_FILT: C28.1, IC8.4 (HINW), R29.2
W_L_ENA: R32.1; also elsewhere on the board
W_L_FILT: C32.1, IC8.5 (!LINW), R32.2
W_OUT: C41.2, IC8.25 (W), L7.1

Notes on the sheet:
+5V LDO (Hi-Pot)
IPM Module
Glitch Filters
Motor Connector
Zener Diode only populated, when Secondary regulation is used
Bypassing: put close to VDD Pins

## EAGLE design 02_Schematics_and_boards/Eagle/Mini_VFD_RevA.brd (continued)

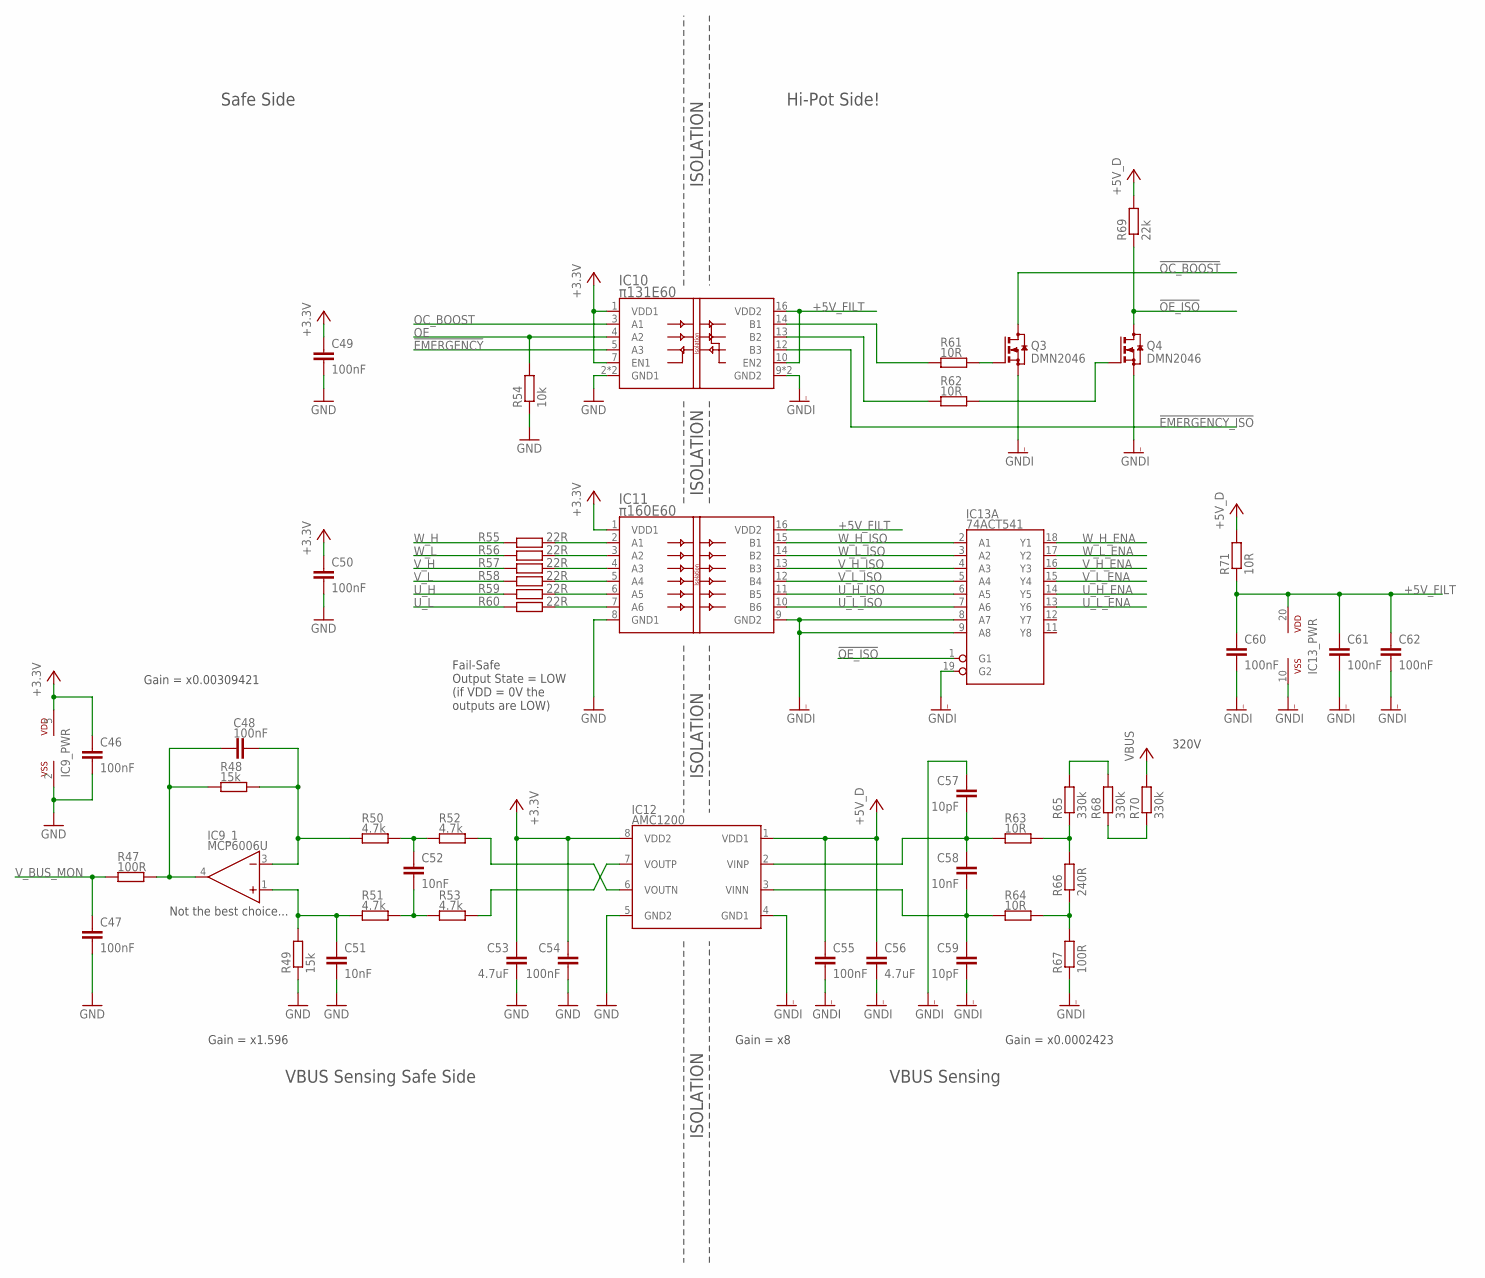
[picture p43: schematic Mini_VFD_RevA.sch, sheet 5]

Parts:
C46, C47, C48, C49, C50, C54, C55, C60, C61, C62: 100nF; C0603
C51, C52, C58: 10nF; C0603
C53, C56: 4.7uF; C0603
C57, C59: 10pF; C0603
IC9: MCP6006U; SOT23-5
IC10: π131E60; SOIC16R
IC11: π160E60; SOIC16R
IC12: AMC1200; SOIC8_W
IC13: 74ACT541; SOIC20NS
Q3, Q4: DMN2046; SOT23
R47, R67: 100R; R0603
R48, R49: 15k; R0603
R50, R51, R52, R53: 4.7k; R0603
R54: 10k; R0603
R55, R56, R57, R58, R59, R60: 22R; R0603
R61, R62, R63, R64, R71: 10R; R0603
R65, R68, R70: 330k; R1206
R66: 240R; R0603
R69: 22k; R0603

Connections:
!EMERGENCY: IC10.5 (A3); also elsewhere on the board
!EMERGENCY_ISO: IC10.12 (B3); also elsewhere on the board
!OC_BOOST: Q3.3 (D); also elsewhere on the board
!OE_ISO: IC13.1 (G1), Q4.3 (D), R69.1
+3.3V: C46.1, C49.1, C50.1, C53.1, C54.1, IC9.5 (VDD), IC10.1 (VDD1), IC10.7 (EN1), IC11.1 (VDD1), IC12.8 (VDD2); also elsewhere on the board
+5V_D: C55.1, C56.1, IC12.1 (VDD1), R69.2, R71.2; also elsewhere on the board
+5V_FILT: C60.1, C61.1, C62.1, IC10.10 (EN2), IC10.16 (VDD2), IC11.16 (VDD2), IC13.20 (VDD), R71.1
GND: C46.2, C47.2, C49.2, C50.2, C51.2, C53.2, C54.2, IC9.2 (VSS), IC10.2 (GND1), IC10.8 (GND1), IC11.8 (GND1), IC12.5 (GND2), R49.1, R54.1; also elsewhere on the board
GNDI: C55.2, C56.2, C57.1, C59.2, C60.2, C61.2, C62.2, IC10.9 (GND2), IC10.15 (GND2), IC11.9 (GND2), IC12.4 (GND1), IC13.8 (A7), IC13.9 (A8), IC13.10 (VSS), IC13.19 (G2), Q3.2 (S), Q4.2 (S), R67.1; also elsewhere on the board
unnamed: Q3.1 (G), R61.2
unnamed: IC12.6 (VOUTN), R52.1
unnamed: IC11.2 (A1), R55.2
unnamed: IC11.3 (A2), R56.2
unnamed: IC11.4 (A3), R57.2
unnamed: IC10.14 (B1), R61.1
unnamed: R64.1, R66.1, R67.2
unnamed: IC11.5 (A4), R58.2
unnamed: IC10.13 (B2), R62.1
unnamed: IC11.6 (A5), R59.2
unnamed: IC11.7 (A6), R60.2
unnamed: Q4.1 (G), R62.2
unnamed: R68.1, R70.1
unnamed: R65.2, R68.2
unnamed: IC12.7 (VOUTP), R53.1
unnamed: C52.1, R50.1, R52.2
unnamed: C52.2, R51.1, R53.2
unnamed: C48.2, IC9.3 (-IN), R48.1, R50.2
unnamed: C51.1, IC9.1 (+IN), R49.2, R51.2
unnamed: C48.1, IC9.4 (OUT), R47.1, R48.2
OC_BOOST: IC10.3 (A1); also elsewhere on the board
OE: IC10.4 (A2), R54.2; also elsewhere on the board
U_H: R59.1; also elsewhere on the board
U_H_ENA: IC13.14 (Y5); also elsewhere on the board
U_H_ISO: IC11.11 (B5), IC13.6 (A5)
U_L: R60.1; also elsewhere on the board
U_L_ENA: IC13.13 (Y6); also elsewhere on the board
U_L_ISO: IC11.10 (B6), IC13.7 (A6)
VBUS: R70.2; also elsewhere on the board
VBUS_MON: C57.2, C58.1, IC12.2 (VINP), R63.2
VBUS_MON_ATT: R63.1, R65.1, R66.2
VBUS_MON_NEG: C58.2, C59.1, IC12.3 (VINN), R64.2
V_BUS_MON: C47.1, R47.2; also elsewhere on the board
V_H: R57.1; also elsewhere on the board
V_H_ENA: IC13.16 (Y3); also elsewhere on the board
V_H_ISO: IC11.13 (B3), IC13.4 (A3)
V_L: R58.1; also elsewhere on the board
V_L_ENA: IC13.15 (Y4); also elsewhere on the board
V_L_ISO: IC11.12 (B4), IC13.5 (A4)
W_H: R55.1; also elsewhere on the board
W_H_ENA: IC13.18 (Y1); also elsewhere on the board
W_H_ISO: IC11.15 (B1), IC13.2 (A1)
W_L: R56.1; also elsewhere on the board
W_L_ENA: IC13.17 (Y2); also elsewhere on the board
W_L_ISO: IC11.14 (B2), IC13.3 (A2)

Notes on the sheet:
Fail-Safe Output State = LOW (if VDD = 0V the outputs are LOW)
ISOLATION
Gain = x8
320V
Gain = x0.0002423
Safe Side
Hi-Pot Side!
VBUS Sensing
VBUS Sensing Safe Side
Not the best choice...
Gain = x1.596
Gain = x0.00309421

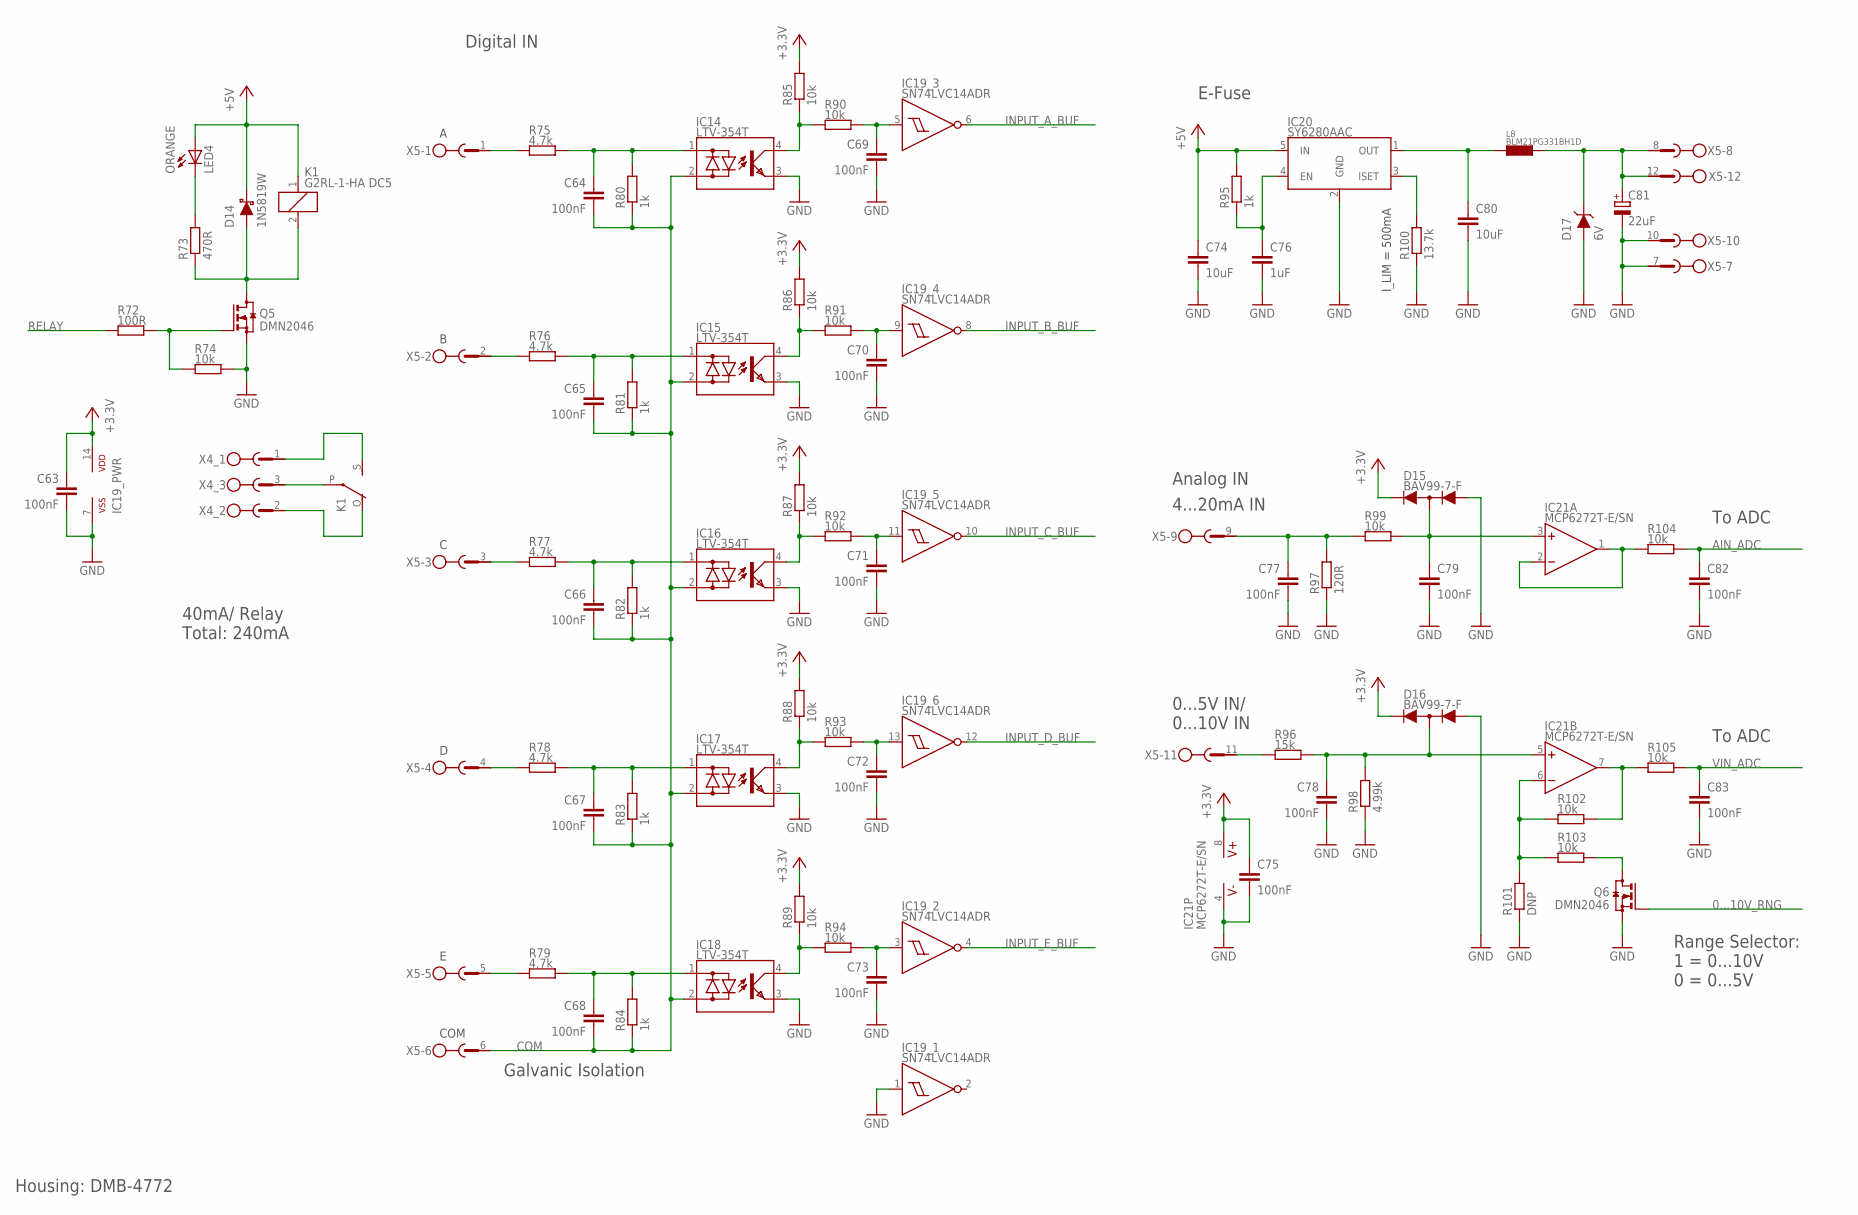
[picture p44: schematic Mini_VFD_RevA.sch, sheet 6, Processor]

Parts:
C63, C64, C65, C66, C67, C68, C69, C70, C71, C72, C73, C75, C77, C78, C79, C82, C83: 100nF; C0603
C74, C80: 10uF; C0805
C76: 1uF; C0603
C81: 22uF; E2-5
D14: 1N5819W; SOD123
D15, D16: BAV99-7-F; SOT23
D17: 6V; DO214AC
IC14, IC15, IC16, IC17, IC18: LTV-354T; SOP04
IC19: SN74LVC14ADR; SO14
IC20: SY6280AAC; SOT23-5
IC21: MCP6272T-E/SN; SO08
K1: G2RL-1-HA DC5; E3206S
L8: BLM21PG331BH1D; R0805
LED4: ORANGE; LED_0603
Q5, Q6: DMN2046; SOT23
R72: 100R; R0603
R73: 470R; R0603
R74, R85, R86, R87, R88, R89, R90, R91, R92, R93, R94, R99, R102, R103, R104, R105: 10k; R0603
R75, R76, R77, R78, R79: 4.7k; R0805
R80, R81, R82, R83, R84, R95: 1k; R0603
R96: 15k; R0603
R97: 120R; R1206
R98: 4.99k; R0603
R100: 13.7k; R0603
R101: DNP; R0603
X4: MSTBV3
X5: MSTBV12

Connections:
0...10V_RNG: Q6.1 (G); also elsewhere on the board
!INPUT_A: IC14.4 (C), R85.1, R90.1
!INPUT_A_FILT: C69.1, IC19.5 (I), R90.2
!INPUT_B: IC15.4 (C), R86.1, R91.1
!INPUT_B_FILT: C70.1, IC19.9 (I), R91.2
!INPUT_C: IC16.4 (C), R87.1, R92.1
!INPUT_C_FILT: C71.1, IC19.11 (I), R92.2
!INPUT_D: IC17.4 (C), R88.1, R93.1
!INPUT_D_FILT: C72.1, IC19.13 (I), R93.2
!INPUT_E: IC18.4 (C), R89.1, R94.1
!INPUT_E_FILT: C73.1, IC19.3 (I), R94.2
+3.3V: C63.1, C75.1, D15.2 (C), D16.2 (C), IC19.14 (VDD), IC21.8 (V+), R85.2, R86.2, R87.2, R88.2, R89.2; also elsewhere on the board
+5V: C74.1, D14.1 (C), IC20.5 (IN), K1.1, LED4.A, R95.2; also elsewhere on the board
+5V_OUT: C81.+, D17.C, L8.2, X5.8, X5.12
AIN_ADC: C82.1, R104.2; also elsewhere on the board
COM: C64.2, C65.2, C66.2, C67.2, C68.2, IC14.2 (AC2), IC15.2 (AC2), IC16.2 (AC2), IC17.2 (AC2), IC18.2 (AC2), R80.1, R81.1, R82.1, R83.1, R84.1, X5.6
GND: C63.2, C69.2, C70.2, C71.2, C72.2, C73.2, C74.2, C75.2, C76.2, C77.2, C78.2, C79.2, C80.2, C81.-, C82.2, C83.2, D15.1 (A), D16.1 (A), D17.A, IC14.3 (E), IC15.3 (E), IC16.3 (E), IC17.3 (E), IC18.3 (E), IC19.1 (I), IC19.7 (VSS), IC20.2 (GND), IC21.4 (V-), Q5.2 (S), Q6.2 (S), R74.2, R97.1, R98.1, R100.1, R101.1, X5.7, X5.10; also elsewhere on the board
INPUT_A_BUF: IC19.6 (O); also elsewhere on the board
INPUT_B_BUF: IC19.8 (O); also elsewhere on the board
INPUT_C_BUF: IC19.10 (O); also elsewhere on the board
INPUT_D_BUF: IC19.12 (O); also elsewhere on the board
INPUT_E_BUF: IC19.4 (O); also elsewhere on the board
IN_A: R75.1, X5.1
IN_A_OPTO: C64.1, IC14.1 (AC1), R75.2, R80.2
IN_B: R76.1, X5.2
IN_B_OPTO: C65.1, IC15.1 (AC1), R76.2, R81.2
IN_C: R77.1, X5.3
IN_C_OPTO: C66.1, IC16.1 (AC1), R77.2, R82.2
IN_D: R78.1, X5.4
IN_D_OPTO: C67.1, IC17.1 (AC1), R78.2, R83.2
IN_E: R79.1, X5.5
IN_E_OPTO: C68.1, IC18.1 (AC1), R79.2, R84.2
unnamed: LED4.C, R73.2
unnamed: C77.1, R97.2, R99.1, X5.9
unnamed: IC20.3 (ISET), R100.2
unnamed: C79.1, D15.3 (AC), IC21.3 (+IN), R99.2
unnamed: C76.1, IC20.4 (EN), R95.1
unnamed: IC21.1 (OUT), IC21.2 (-IN), R104.1
unnamed: C78.1, D16.3 (AC), IC21.5 (+IN), R96.2, R98.2
unnamed: R96.1, X5.11
unnamed: IC21.7 (OUT), R102.2, R105.1
unnamed: IC21.6 (-IN), R101.2, R102.1, R103.2
unnamed: Q6.3 (D), R103.1
unnamed: C80.1, IC20.1 (OUT), L8.1
unnamed: K1.P, X4.3
unnamed: K1.O, X4.2
unnamed: K1.S, X4.1
RELAY: R72.1; also elsewhere on the board
RELAY_DRAIN: D14.2 (A), K1.2, Q5.3 (D), R73.1
RELAY_R: Q5.1 (G), R72.2, R74.1
VIN_ADC: C83.1, R105.2; also elsewhere on the board

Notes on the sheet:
Housing: DMB-4772
40mA/ Relay Total: 240mA
I_LIM = 500mA
COM
Digital IN
Analog IN
4...20mA IN
0...5V IN/ 0...10V IN
Range Selector: 1 = 0...10V 0 = 0...5V
To ADC
Galvanic Isolation
E-Fuse

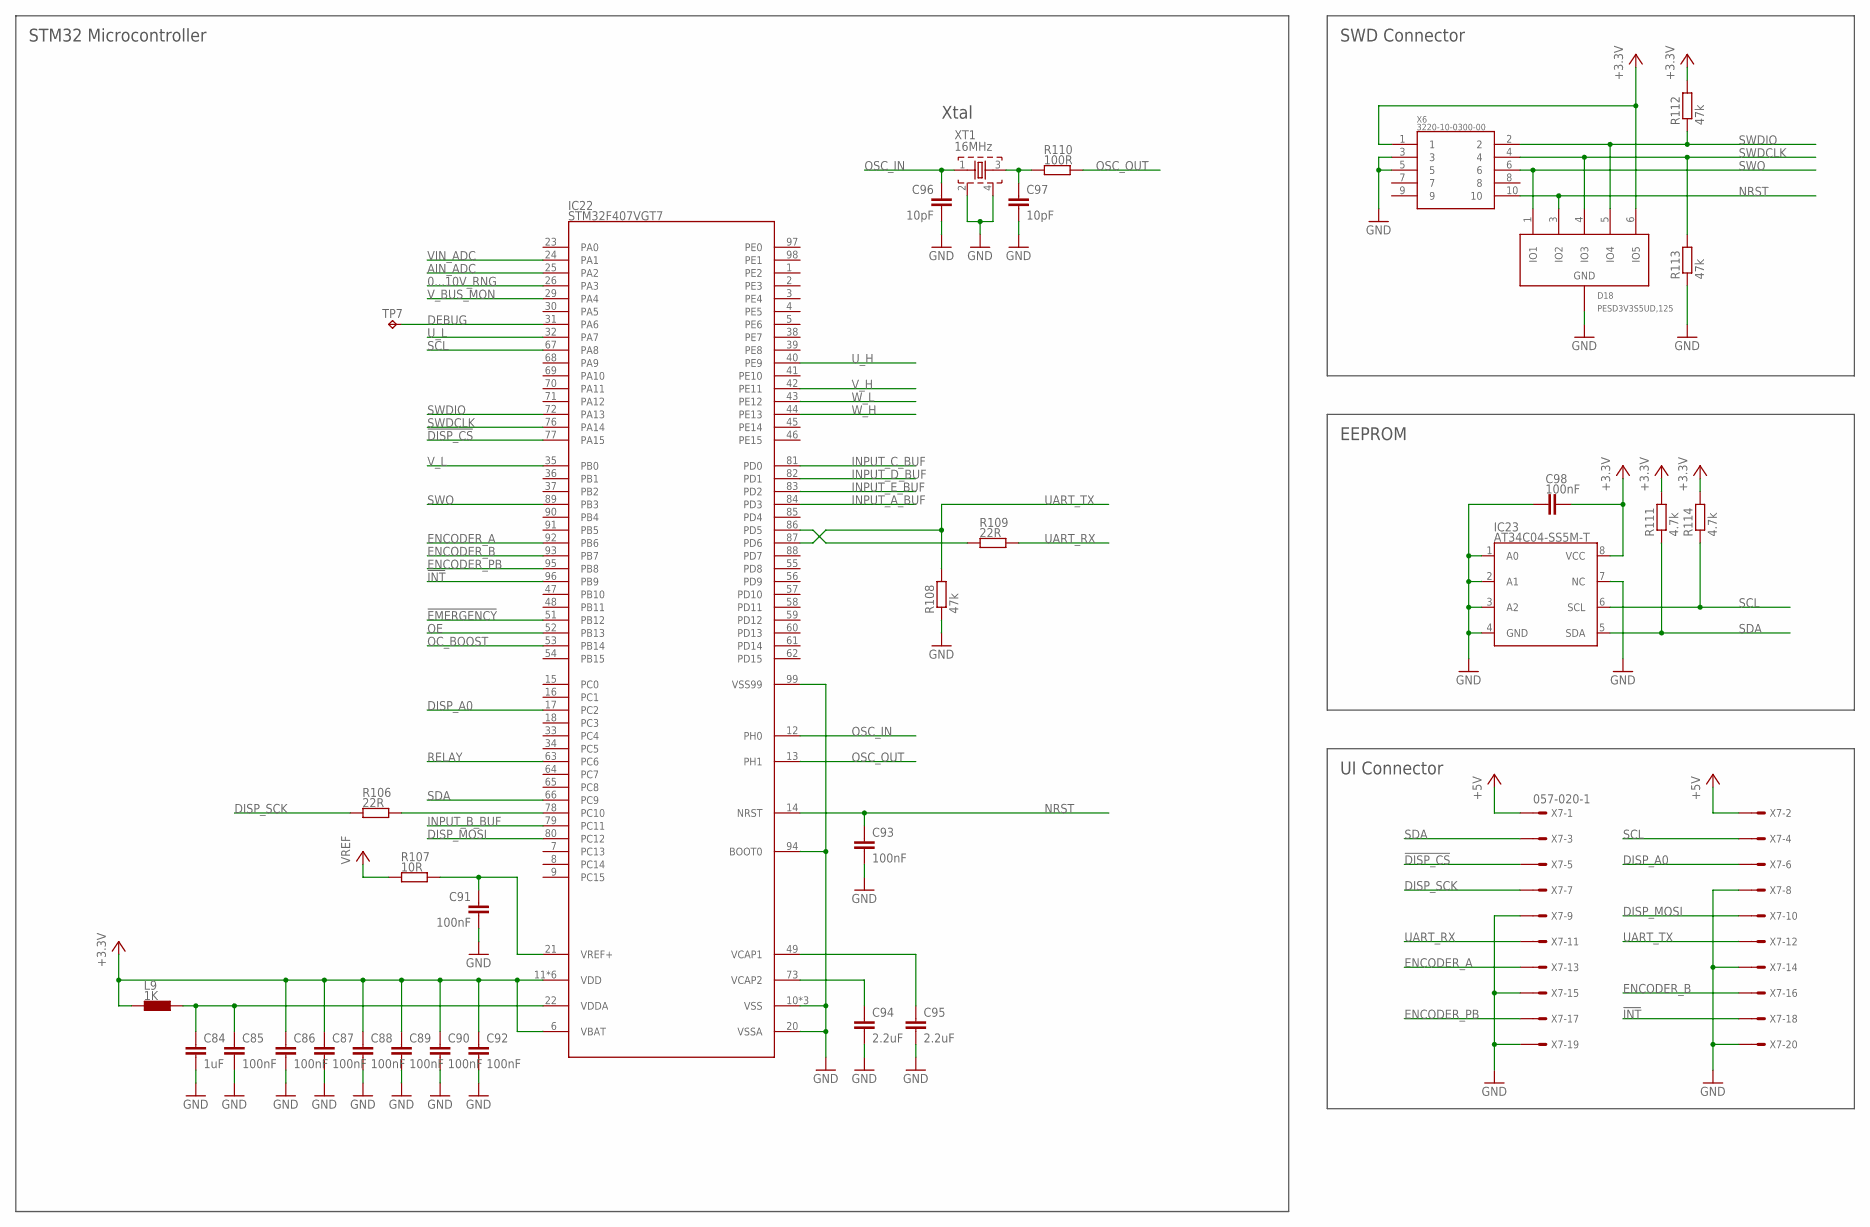
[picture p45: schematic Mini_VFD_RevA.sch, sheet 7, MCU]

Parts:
C84: 1uF; C0603
C85, C86, C87, C88, C89, C90, C91, C92, C93, C98: 100nF; C0603
C94, C95: 2.2uF; C0603
C96, C97: 10pF; C0603
D18: PESD3V3S5UD,125; TSOP-6
IC22: STM32F407VGT7; LQFP100
IC23: AT34C04-SS5M-T; SOIC8
L9: 1K; R0603
R106, R109: 22R; R0603
R107: 10R; R0603
R108, R112, R113: 47k; R0603
R110: 100R; R0603
R111, R114: 4.7k; R0603
TP7: TP_SOLDREYE; SOLDER_EYE
X6: 3220-10-0300-00
X7: 057-020-1
XT1: 16MHz; 3225_4P

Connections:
0...10V_RNG: IC22.26 (PA3); also elsewhere on the board
!DISP_CS: IC22.77 (PA15), X7.5
!EMERGENCY: IC22.51 (PB12); also elsewhere on the board
!INT: IC22.96 (PB9), X7.18
+3.3V: C86.1, C87.1, C88.1, C89.1, C90.1, C92.1, C98.2, D18.6 (IO5), IC22.6 (VBAT), IC22.11 (VDD), IC22.19 (VDD), IC22.28 (VDD), IC22.50 (VDD), IC22.75 (VDD), IC22.100 (VDD), IC23.8 (VCC), L9.2, R111.2, R112.2, R114.2, X6.1; also elsewhere on the board
+3.3V_FILT: C84.1, C85.1, IC22.22 (VDDA), L9.1
+5V: X7.1, X7.2; also elsewhere on the board
AIN_ADC: IC22.25 (PA2); also elsewhere on the board
DEBUG: IC22.31 (PA6), TP7.1
DISP_A0: IC22.17 (PC2), X7.6
DISP_MOSI: IC22.80 (PC12), X7.10
DISP_SCK: R106.1, X7.7
ENCODER_A: IC22.92 (PB6), X7.13
ENCODER_B: IC22.93 (PB7), X7.16
ENCODER_PB: IC22.95 (PB8), X7.17
GND: C84.2, C85.2, C86.2, C87.2, C88.2, C89.2, C90.2, C91.2, C92.2, C93.2, C94.2, C95.2, C96.2, C97.2, C98.1, D18.2 (GND), IC22.10 (VSS), IC22.20 (VSSA), IC22.27 (VSS), IC22.74 (VSS), IC22.94 (BOOT0), IC22.99 (VSS99), IC23.1 (A0), IC23.2 (A1), IC23.3 (A2), IC23.4 (GND), IC23.7 (NC), R108.1, R113.1, X6.3, X6.5, X7.8, X7.9, X7.14, X7.15, X7.19, X7.20, XT1.2, XT1.4; also elsewhere on the board
INPUT_A_BUF: IC22.84 (PD3); also elsewhere on the board
INPUT_B_BUF: IC22.79 (PC11); also elsewhere on the board
INPUT_C_BUF: IC22.81 (PD0); also elsewhere on the board
INPUT_D_BUF: IC22.82 (PD1); also elsewhere on the board
INPUT_E_BUF: IC22.83 (PD2); also elsewhere on the board
unnamed: IC22.78 (PC10), R106.2
unnamed: IC22.86 (PD5), R109.1
unnamed: C94.1, IC22.73 (VCAP2)
unnamed: C95.1, IC22.49 (VCAP1)
unnamed: C97.1, R110.1, XT1.3
unnamed: C91.1, IC22.21 (VREF+), R107.2
NRST: C93.1, D18.3 (IO2), IC22.14 (NRST), X6.10
OC_BOOST: IC22.53 (PB14); also elsewhere on the board
OE: IC22.52 (PB13); also elsewhere on the board
OSC_IN: C96.1, IC22.12 (PH0), XT1.1
OSC_OUT: IC22.13 (PH1), R110.2
RELAY: IC22.63 (PC6); also elsewhere on the board
SCL: IC22.67 (PA8), IC23.6 (SCL), R114.1, X7.4
SDA: IC22.66 (PC9), IC23.5 (SDA), R111.1, X7.3
SWDCLK: D18.4 (IO3), IC22.76 (PA14), R113.2, X6.4
SWDIO: D18.5 (IO4), IC22.72 (PA13), R112.1, X6.2
SWO: D18.1 (IO1), IC22.89 (PB3), X6.6
UART_RX: R109.2, X7.11
UART_TX: IC22.87 (PD6), R108.2, X7.12
U_H: IC22.40 (PE9); also elsewhere on the board
U_L: IC22.32 (PA7); also elsewhere on the board
VIN_ADC: IC22.24 (PA1); also elsewhere on the board
VREF: R107.1; also elsewhere on the board
V_BUS_MON: IC22.29 (PA4); also elsewhere on the board
V_H: IC22.42 (PE11); also elsewhere on the board
V_L: IC22.35 (PB0); also elsewhere on the board
W_H: IC22.44 (PE13); also elsewhere on the board
W_L: IC22.43 (PE12); also elsewhere on the board

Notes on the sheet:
SWD Connector
STM32 Microcontroller
UI Connector
EEPROM
Xtal



Board: 2 copper layers, 110.0 x 190.0 mm, 308 parts (16 on the bottom side), 195 nets.

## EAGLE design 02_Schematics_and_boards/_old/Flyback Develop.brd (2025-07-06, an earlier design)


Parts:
C1, C2: 1uF; C102-082X133
C3: 68uF/450V; E7,5-18
C4, C11: 10uF/450V; E3,5-10
C5: 390nF; C0603
C6: 5.6nF; C0603
C7: 10uF; E2,5-5
C8: 47uF; E2,5-7
C9: 470uF; E3,5-8
C10: 22uF; E2-5
CY1, CY2: CYYC7B5; YC7B5
CY3: 2.2nF; YC7B5
D1, D2, D3, D4, D5: STTH3R04U; SMB
D6, D9, D10: PU1JA; DO214AC
D7: SMBJP6KE200A-TP; DO214AC
D8: BAT54J; SOD123
F1: 2A; 2010-FUSE
H1, H2, H3, H4: MOUNT-PAD-ROUND3.2; 3,2-PAD
IC1: VIPER06HN; DIL07
L1: 20mH; CMC_SLT
L2: 1mH; SLH0704
L3: 10uH; COIL_4X4
LED1, LED2: LED_0805
R1: 10D561K; S10K175
R2, R3, R4, R5, R6, R7: 220k; R1210
R8: 6.8k; R0603
R9: 22k; R0603
R10: 10R; R0805
R11: 36k; R0603
R12: 10k; R0603
R13: 4.7k; R0603
T1: 750370024; WE-OLSTM_EE13_L13.72W20.45H10.8
TP1, TP2, TP3, TP4, TP5, TP6: TP_SOLDREYE; SOLDER_EYE
X1: MSTBV3
X2, X3: CON_2_2.54; 1X02

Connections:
+12V: C10.+, L3.1, R13.2, TP5.1, X3.2
+15V: C8.+, D8.2 (A), D9.C, R11.2, X2.2
+HV: C4.+, D7.A, L2.1, T1.3, TP4.1
GND: C9.-, C10.-, CY3.2, LED2.C, T1.6, TP6.1, X3.1
GNDI: C3.-, C4.-, C5.2, C6.2, C7.-, C8.-, C11.-, CY3.1, D2.A, D4.A, IC1.1 (GND), LED1.C, R9.1, R12.1, T1.4, TP2.1, TP3.1, X2.1
L': C1.1, F1.P$2 (2), L1.OUT1, R1.2, R2.2
N: C1.2, L1.OUT2, R1.1, R4.1, X1.2
unnamed: D6.C, D7.C
unnamed: R5.1, R6.2
unnamed: R6.1, R7.2
unnamed: LED1.A, R7.1
unnamed: C9.+, D10.C, L3.2
unnamed: LED2.A, R13.1
unnamed: C11.+, D5.C, L2.2
unnamed: C2.2, CY2.2, D3.A, D4.C, L1.IN2
unnamed: F1.P$1 (1), X1.1
unnamed: R2.1, R3.2
unnamed: R3.1, R4.2
unnamed: D10.A, T1.9
unnamed: D6.A, IC1.7 (DRAIN), IC1.8 (DRAIN), T1.1
unnamed: C5.1, R8.1
unnamed: D8.1 (C), R10.2
unnamed: C7.+, IC1.2 (VDD), R10.1
unnamed: IC1.3 (LIM), R9.2
unnamed: D9.A, T1.5
unnamed: IC1.4 (FB), R11.1, R12.2
unnamed: C6.1, IC1.5 (COMP), R8.2
unnamed: C2.1, CY1.1, D1.A, D2.C, L1.IN1
PE: CY1.2, CY2.1, X1.3
V_BUS: C3.+, D1.C, D3.C, D5.A, R5.2, TP1.1

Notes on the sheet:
LCSC: C273582
3.3V REF


Board: 2 copper layers, 68.0 x 76.5 mm, 58 parts (0 on the bottom side), 30 nets.

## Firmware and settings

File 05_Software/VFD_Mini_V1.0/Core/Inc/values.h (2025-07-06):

/*
 * values.h
 *
 *  Created on: Jan 27, 2025
 *      Author: Michael Adam
 *      E-Mail: michael.adam4@proton.me
 */

#ifndef INC_VALUES_H_
#define INC_VALUES_H_

// Includes
#include "main.h"
#include "eeprom.h"

// Defines
#define DEFAULT_MOTOR_FREQ_NOMINAL		500
#define DEFAULT_MAX_FREQUENCY 			1200	// 120Hz
#define DEFAULT_MIN_FREQUENCY 			50		// 5Hz
#define DEFAULT_MOTOR_VOLT_NOMINAL		230
#define DEFAULT_MOTOR_RATE_ACC			10
#define DEFAULT_MOTOR_RATE_DEC			10

#define PARAMETER_COUNT					18

#define EEPROM_DEV_ADDR					M24C02_ADDR_0

// Enumerators
enum
{
	MOTOR_STATE_STOP = 0, MOTOR_STATE_FWD, MOTOR_STATE_REV, MOTOR_STATE_ERROR
};

// Typedefs
typedef struct
{
	char parameter_string[15];
	uint16_t parameter_val;
	uint16_t default_val;
	uint16_t max_val;
	uint8_t eeprom_addr;
} parameter;

// Variables
extern uint8_t motor_enable;
extern uint8_t motor_status;
extern uint8_t parameter_changed_flag;
//extern uint16_t set_voltage;
extern float bus_voltage_meas;
extern uint16_t p00_freq_nominal;
extern uint16_t p01_voltage_nominal;
extern uint16_t p02_freq_minimal;
extern uint16_t p03_freq_maximal;
extern uint16_t p04_accel_rate;
extern uint16_t p05_decel_rate;
extern uint8_t p06_freq_source;
extern uint8_t p07_stop_mode;
extern uint8_t p08_in_a_function;
extern uint8_t p09_in_b_function;
extern uint8_t p10_in_c_function;
extern uint8_t p11_in_d_function;
extern uint8_t p12_in_e_function;
extern uint8_t p13_reverse_forbid;
extern uint8_t p14_analog_in_range;
extern uint16_t p15_jump_freq;
extern uint8_t p16_jump_rng;

extern uint16_t motor_voltage_temp;
extern uint16_t adc_freq_raw;

extern uint16_t actual_frequency_display;
extern float amplitude_divider_display;

extern uint8_t emergency_off;

// Pushbutton Flags
extern uint8_t pb_pressed_fwd;
extern uint8_t pb_pressed_rev;
extern uint8_t pb_pressed_stop;
extern uint8_t pb_pressed_menu;


// DEBUG
extern uint16_t set_frequency;
extern uint16_t ampl_div;

// Typedefs
extern parameter param[PARAMETER_COUNT];  // Array of 50 parameter structures

// Function prototypes
ErrorStatus Values_Init(void);

#endif /* INC_VALUES_H_ */

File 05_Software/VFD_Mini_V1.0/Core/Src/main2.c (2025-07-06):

/*
 * main2.c
 *
 *  Created on: Jan 27, 2025
 *      Author: Michael Adam
 *      E-Mail: michael.adam4@proton.me
 */

// Includes
#include "main.h"
#include "vfd.h"
#include "dogl128.h"
#include "fonts.h"
#include "mgui.h"
#include "menu.h"
#include "eeprom.h"
#include "values.h"
#include "adc.h"
#include "tca9534.h"
#include "gpio.h"
#include "diagnosis.h"

// Defines
#define STARTUP_DELAY				1500

// Variables

extern IWDG_HandleTypeDef hiwdg;

uint8_t tca9534_ready = 1;

uint32_t main_clk_freq;

// Functions
// Init
void Init(void)
{
	uint32_t init_delay_counter = HAL_GetTick() + STARTUP_DELAY;
	uint32_t display_delay_counter = HAL_GetTick() + 500;
	main_clk_freq = HAL_RCC_GetSysClockFreq();

	GPIO_Init();

	VFD_Init();

	if (Values_Init() != SUCCESS)
	{
		Display_Fill(Display_COLOR_BLACK);
		Display_GotoXY(2, 2);
		Display_Puts("EEPROM ERROR", &Font_7x10, Display_COLOR_WHITE);
	}

	if (TCA9534_Init(TCA9534_ADDR_0, IO_EXPANDER_DIRECTION) != SUCCESS)
	{
		Display_Fill(Display_COLOR_BLACK);
		Display_GotoXY(2, 14);
		Display_Puts("IO_EXPANDER ERROR", &Font_7x10, Display_COLOR_WHITE);
		tca9534_ready = 0;
	}

	if (ADC_Init() != SUCCESS)
	{
		Display_Fill(Display_COLOR_BLACK);
		Display_GotoXY(2, 26);
		Display_Puts("ADC_REF ERROR", &Font_7x10, Display_COLOR_WHITE);
	}

	do
	{
		HAL_IWDG_Refresh(&hiwdg);
		if (display_delay_counter < HAL_GetTick())
		{
			display_delay_counter = 0;
		}
	} while (display_delay_counter);

	Display_Init();
	Menu_Init();
	Display_UpdateScreen();

	do
	{
		HAL_IWDG_Refresh(&hiwdg);
		if (init_delay_counter < HAL_GetTick())
		{
			init_delay_counter = 0;
		}
	} while (init_delay_counter);

	// Clear display
	Display_Clear();

	if (tca9534_ready)
	{
		Write_4LED(0,0,1,0);
	}
}

// Main Loop
void Loop(void)
{
	// Values
	uint8_t menu_mode_enabled = 0;
	uint8_t pb_pressed_menu_old = 0;
	uint8_t set_direction = SET_STOP;
	uint16_t pb_menu_counter = 0;
	uint32_t tick_counter = HAL_GetTick() + 100;


	// Main While Loop
	while (1)
	{
		// Refresh IWDG Timer
		HAL_IWDG_Refresh(&hiwdg);

		// VFD Handler
		VFD_Handler(set_frequency, set_direction);

		// IO Expander Routine
		if (tca9534_ready)
		{
			Read_PB_All();

			if(pb_pressed_stop || emergency_off)
			{
				Write_4LED(0, 0, 1, menu_mode_enabled);
				motor_status = MOTOR_STATE_STOP;
				set_direction = SET_STOP;
			}
			else
			{
				if (pb_pressed_fwd)
				{
					Write_4LED(1, 0, 0, menu_mode_enabled);
					motor_status = MOTOR_STATE_FWD;
					set_direction = SET_DIR_FWD;
				}
				if (pb_pressed_rev)
				{
					Write_4LED(0, 1, 0, menu_mode_enabled);
					motor_status = MOTOR_STATE_REV;
					set_direction = SET_DIR_REV;
				}
			}

			if(pb_pressed_menu)
			{
				if(pb_pressed_menu != pb_pressed_menu_old)
				{
					menu_mode_enabled = !menu_mode_enabled;
					Write_LED(menu_mode_enabled, LED_MENU);
					pb_menu_counter++;
					if(pb_menu_counter)
					{
						//debug mode here
					}
				}
			}
			else
			{
				pb_menu_counter = 0;
			}

			pb_pressed_menu_old = pb_pressed_menu;

			pb_pressed_fwd = 0;
			pb_pressed_rev = 0;
			pb_pressed_stop = 0;
			pb_pressed_menu = 0;

		}
		else
		{
			if (emergency_off)
			{
				motor_status = MOTOR_STATE_STOP;
				set_direction = SET_STOP;
			}
		}

		GPIO_Relay_Handler(RELAY_MODE_OFF);

		Menu_Encoder_Handler(menu_mode_enabled);

		Menu_Handler(menu_mode_enabled);

		Display_UpdateScreen();

		Diag_Check_Reference();

		do
		{
			if (tick_counter < HAL_GetTick())
			{
				tick_counter = 0;
			}
		} while (tick_counter);

		tick_counter = HAL_GetTick() + 100;
	}
}

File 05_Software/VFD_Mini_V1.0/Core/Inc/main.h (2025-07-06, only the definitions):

#define DISP_RS_Pin GPIO_PIN_2
#define DISP_RS_GPIO_Port GPIOC
#define V_ADC_Pin GPIO_PIN_1
#define V_ADC_GPIO_Port GPIOA
#define MA_ADC_Pin GPIO_PIN_2
#define MA_ADC_GPIO_Port GPIOA
#define IN_RANGE_Pin GPIO_PIN_3
#define IN_RANGE_GPIO_Port GPIOA
#define V_BUS_MON_Pin GPIO_PIN_4
#define V_BUS_MON_GPIO_Port GPIOA
#define DEBUG_Pin GPIO_PIN_6
#define DEBUG_GPIO_Port GPIOA
#define EMERGENCY_Pin GPIO_PIN_12
#define EMERGENCY_GPIO_Port GPIOB
#define OE_Pin GPIO_PIN_13
#define OE_GPIO_Port GPIOB
#define OC_BOOST_Pin GPIO_PIN_14
#define OC_BOOST_GPIO_Port GPIOB
#define RELAY_Pin GPIO_PIN_6
#define RELAY_GPIO_Port GPIOC
#define SPI_CS_Pin GPIO_PIN_15
#define SPI_CS_GPIO_Port GPIOA
#define INPUT_B_BUF_Pin GPIO_PIN_11
#define INPUT_B_BUF_GPIO_Port GPIOC
#define INPUT_C_BUF_Pin GPIO_PIN_0
#define INPUT_C_BUF_GPIO_Port GPIOD
#define INPUT_D_BUF_Pin GPIO_PIN_1
#define INPUT_D_BUF_GPIO_Port GPIOD
#define INPUT_E_BUF_Pin GPIO_PIN_2
#define INPUT_E_BUF_GPIO_Port GPIOD
#define INPUT_A_BUF_Pin GPIO_PIN_3
#define INPUT_A_BUF_GPIO_Port GPIOD
#define ENCODER_PB_Pin GPIO_PIN_8
#define ENCODER_PB_GPIO_Port GPIOB
#define INT_N_Pin GPIO_PIN_9
#define INT_N_GPIO_Port GPIOB

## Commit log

2025-07-06 Init Commit
    [Flyback Develop.brd, Flyback Develop.sch, Mini_VFD_RevA.brd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]
2025-07-08 Edited Documentation
    [Mini_VFD_UI_RevA.brd, Mini_VFD_UI_RevA.sch]

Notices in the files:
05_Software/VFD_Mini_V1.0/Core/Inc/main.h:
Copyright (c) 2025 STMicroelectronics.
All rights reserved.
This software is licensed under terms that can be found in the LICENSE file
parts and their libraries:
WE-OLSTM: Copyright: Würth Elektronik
